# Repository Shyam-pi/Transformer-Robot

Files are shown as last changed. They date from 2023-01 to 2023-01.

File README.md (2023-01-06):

# Transformer-Robot
A novel mobile manipulator with a collapsible arm created for my final project of ENPM662 at the University of Maryland, College Park

Please find the CAD model of the robot in CAD_model.zip 

To run the ROS/URDF package in Gazebo, extract the transformers.zip folder to your catkin workspace, and do the following to build it: 
1. Navigate to your catkin workspace folder, open terminal and enter 'catkin_make' to build the workspace.
2. Enter the following command in your terminal 'source ~/catkin_ws/devel/setup.bash'

Once the building process is done, you can simply launch the package in Gazebo by using the following command in your terminal:
roslaunch transformer template.launch

In order to visualize the feed from the camera, after executing the above command, type 'rviz' in a new terminal window. In your RVIZ, add an 'Image' component, and change the image topic to the available topic, and you can see the video feed from the camera appearing in a window in Rviz.

To launch any of the ROS python scripts, navigate to the scripts folder inside the package, and open a terminal window in that location. Launch any of the available scripts using the below command in terminal 

python3 'script_name.py'

Please take note that you need to use any of the scripts only when Gazebo is running, and terminal window should overlay on top of the Gazebo window.

Following are the description of the available scripts:

1. teleop.py - Use this script to control the mobile base of the robot.
2. publisher.py - It is used to initialize the configuration of the robot. Type 0 followed by the publisher.py to take the robot to collapsed position, and 1 to take it to the extended position.

Please checkout the outputs folder for visualizing the working of the package.

To get comprehensive information on the robot please refer to the report available in the repo.

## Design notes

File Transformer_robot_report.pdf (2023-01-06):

## ENPM662 - Introduction to Robot Modeling

## Project 2 Modeling of Transformer Robot

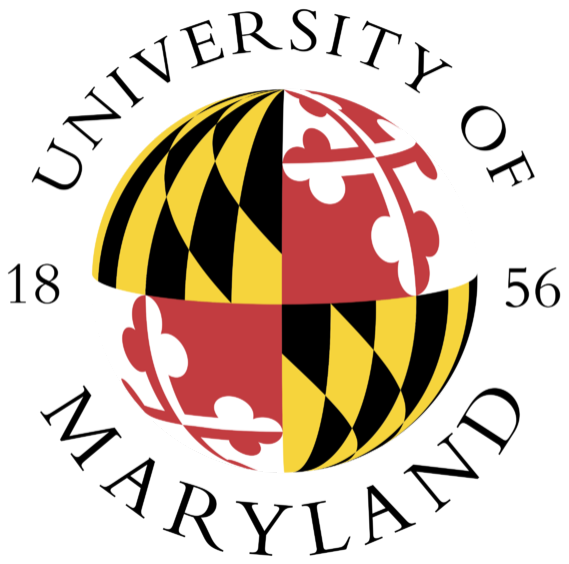
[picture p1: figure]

AUTHOR:
SHYAMSUNDAR PRABHAKAR INDRA UID - 119360842
DIRECTORY ID - SHYAMPI

ii

### ABSTRACT

This project explains the design, control, and simulation of a novel ’Transformer Robot’ which can potentially make a huge difference of how storage systems work, which can especially be a huge game-changer in today’s world with the amount of products being produced everyday. The robot consists of a mobile base and a manipulator arm, which were designed using Solidworks[1] and were exported as a URDF. A ROS[2] package was developed, with transmissions and controllers, and integrated with the URDF. A camera was attached to the end effector of the manipulator arm to visualize the environment. The forward and inverse kinematics of the robot’s arm are calculated and verified. The robot has been simulated and controlled in Gazebo. A simulation of the robot doing a planned task in a custom environment has also been done. The challenges faced and future work planned have been described.

iii

### TABLE OF CONTENTS

iv

### LIST OF ILLUSTRATIONS

Number | Page
1.1 Conventional Forklift in a Storage House[3] | | 2
3.1 Transformer Robot in its extended mode | | 5
3.2 Transformer Robot in its collapsed mode | | 6
3.3 Manipulator Arm extended mode | | 7
3.4 Manipulator Arm collapsed mode | | 7
3.5 Close-Up of End Effector | | 8
4.1 Coordinate Systems assignment | 10
5.1 Representation of case 1 in Gazebo | 13
5.2 FK Validation for Case 1 | 14
5.3 Representation of case 2 in Gazebo | 14
5.4 FK validation for Case 2 | 14
5.5 Initialized Jacobian Matrix and corresponding robot pose | 15
5.6 Trajectory traced using Jacobian in python script | 16
5.7 Variation of joint parameters with time, to achieve the trajectory . . . 16
6.1 Workspace of the Robotic Arm in ’mm’ | 17

C h a p t e r 1

### INTRODUCTION

Mobile Manipulators aren’t a rarity in today’s technologically advanced world. However almost all the mobile manipulators one can come across are pretty tall in z-height, if not for their large overall size. One classical example is that of the Husky UGV with its tall Manipulator arm sticking out.

Contrary to such tall mobile manipulators, a novel ’Transformer Robot’ is being introduced. Getting its name from the famous Transformers cartoon, it is indeed yet another Mobile Manipulator, but quite different. The Transformer Robot has a collapsible arm, i.e., the manipulator arm is custom designed such that in it’s ’collapsed’ state it’s almost in level with the mobile base itself.

Such a robot with a reduced z-height, opens up to a plethora of opportunities. One of the most prominent is the way storage industries work. Conventionally such storage houses have pre-defined long pathways for the forklifts to move in a very inefficient manner as shown in figure 1.1. The Transformer robot can potentially revolutionize the way such storage houses work. When provided with shelves with a gap underneath, the Transform Robot with it’s low-profile could easily navigate through these gaps, hence reducing the distance covered in the to and fro motion to a great level. Though this feels trivial, when looked at this over a period of years and years, this shall save thousands of hours and miles of extra work. This motion efficiency, can boost the energy efficiency of these places as well.

This project report describes the work done in designing, controlling, and simulating the above proposed Transformer Robot. The report is divided into various sections. The introduction provides an overview of the Transformer Robot and its novel applications. The detailed specifications of the Transformer Robot are described in the section titled "The Transformer Robot" The "Kinematics and Kinematic Validation" section covers the forward and inverse kinematics of the robot’s manipulator arm and the validation of the calculations. The "Workspace Study" section discusses the total reach of the arm and the limitations of the space it cannot reach. The "Assumptions" section outlines the assumptions made during the development and design of the Transformer Robot. The "Package, Control Method and Visualization" provides a link to the entire working package itself,

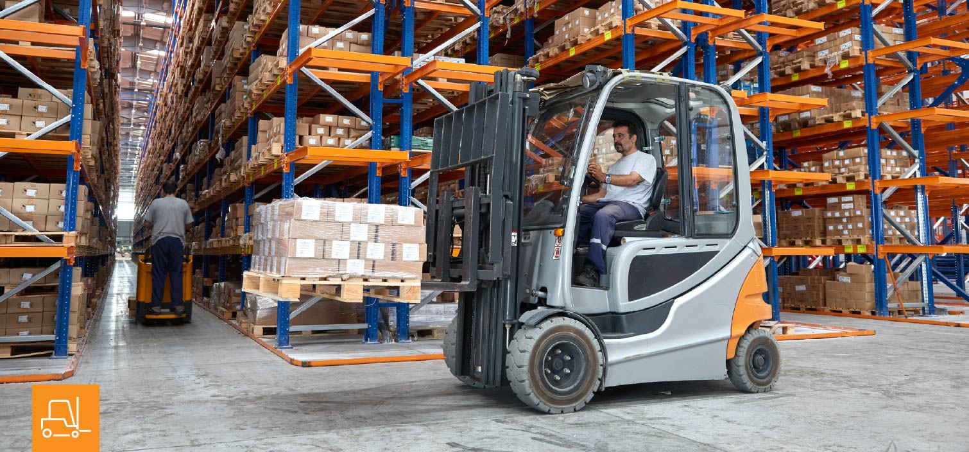
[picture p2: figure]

Figure 1.1: Conventional Forklift in a Storage House[3]

the way the joints in the robots are controlled, and a visualization of the robot performing a specific task. The "Problems Faced and Lessons Learned" section covers the challenges encountered during the project and the lessons learned from them. The "Future Work" section lists potential improvements to the Transformer Robot. The "Conclusion" section summarizes the project, and the "References" section lists the sources used.

C h a p t e r 2

### THE TRANSFORMER ROBOT

This section briefs the proposed design, specifications, and the planned task of the robot being modeled for this project.

### 2.1 Specifications of the Transformer Robot

Mobile Base
Length of the Mobile Base | 0.914 m
Width of the Mobile Base | 0.508 m
Height of the Mobile Base | 0.3 m
Mass (Base + Wheels + Axles) | 82.6 Kg
Wheel Base | 0.508 m
Motion Model | Unicycle
Degrees of Freedom | 3 in total - x, y and yaw.
Manipulator Arm
Height of Arm with all joints extended | 2.388 m
End Effector Used | Simple custom 1 DOF Grasping tool
Degrees of Freedom | 7 in total - Five revolute and one pris-matic, and one DoF for the End Effector
Length of End Effector | 0.09 m

### 2.2 Type of Robot

The type of robot used here is a mobile manipulator. Mobile manipulators are used in several applications all over Earth and even beyond Earth. For example, Husky UGV is a mobile manipulator which is used for all-terrain Robotics research, and a Mars rover is also a type of mobile manipulator. The manipulator arm is a serial manipulator.

### 2.3 Degrees of Freedom of The System

The system has a total of 9 DoF. The mobile base has 3 DoF while the manipulator arm has 5 DoF. The mobile base can move along x and y directions and rotate around the z axis. The arm has 3 revolute joints, with a prismatic joint and revolute joint for the end-effector, and the end-effector itself has 1 DoF.

### 2.4 Application of The Transformer Robot

As the introduction described, the robot is a novel attempt at reforming how storages work. Conventionally, most of the storage houses use forklifts operated by humans, which have to navigate through longer pathways. The central idea behind the Transformer robot is a mobile manipulator being able to reduce the vertical height of itself so that it can easily navigate through remote spaces.

The proposed idea of reformed storage systems is that the shelves have ample space underneath them, enough for the transformer robot to pass through in their collapsed state. This will allow the transformer robot to navigate to the point of interest in the shortest way possible, hence saving thousands and thousands of man-hours and power in the long run.

### 2.5 Motivation for Choosing Transformer Robot

The main motivation was the novelty behind the transformer robot, which enables it to be used as a multi-purpose robot which, as explained before, can be used for efficient pick and place operations and at the same time, owing to its small size in its collapsed state, and can be used for search and rescue operations having acces to remote areas in case of anomalies at the same time.

The project presented an opportunity to create a holistic model right from basic 3D modelling to actually making a simulation of the same. The idea of modelling what was learnt in the theory into an actual working model from scratch was also a great motivation for the choice.

C h a p t e r 3

### CAD MODELS

This section contains pictures of the Transformer Robot assembly and that of the manipulator arm assembly in its two different modes.

### 3.1 The Transformer Robot CAD Model

The model of the Transformer Robot was created from scratch using Solidworks. The Robot’s two modes are shown in figure 3.1 and figure 3.2.

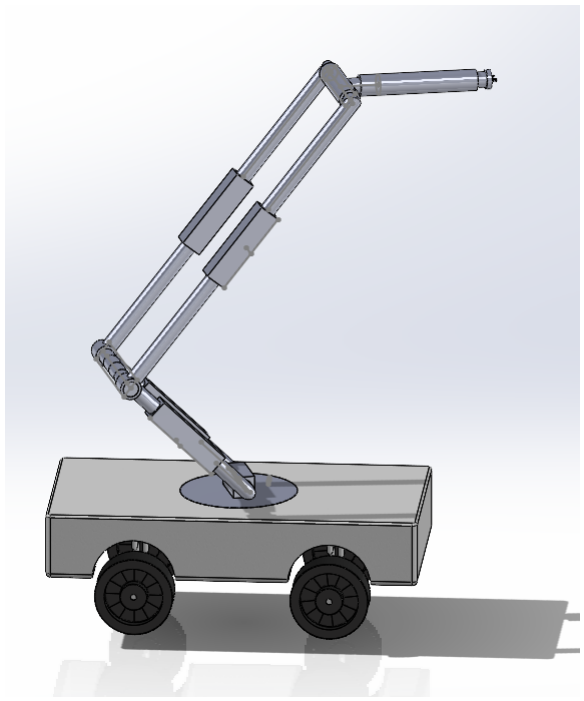
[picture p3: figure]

Figure 3.1: Transformer Robot in its extended mode

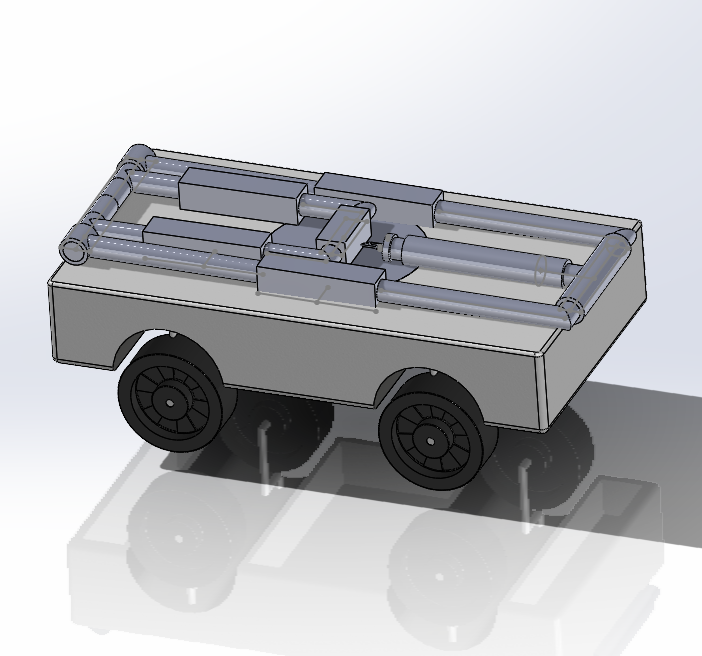
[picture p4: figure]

Figure 3.2: Transformer Robot in its collapsed mode

### 3.2 The Arm Model

This section has two views of the arm model as well as a close up of the custom designed end effector as shown in figure 3.3 and figure 3.4. The arm model has a rotating base which is attached to the mobile base, allowing full freedom of revolution. This joint is followed by three revolute joints with their rotation axis parallel to each other. Hence the arm itself has 6 degrees of freedom. This is followed by a prismatic joint, revolute joint and then the end effector.

The end effector is a simple setup with two fingers, each having a revolute joint tied to each other, hence having 1 DoF in total.

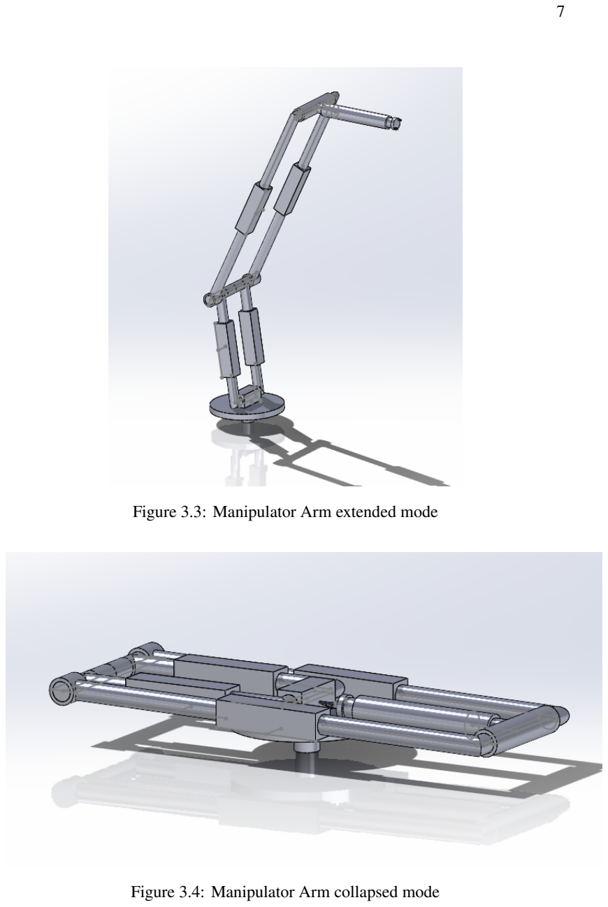
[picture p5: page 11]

Figure 3.3: Manipulator Arm extended mode

Figure 3.4: Manipulator Arm collapsed mode

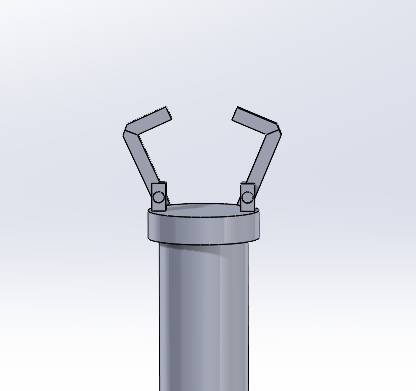
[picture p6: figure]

Figure 3.5: Close-Up of End Effector

C h a p t e r 4

### KINEMATICS

### 4.1 Forward Kinematics

Forward Kinematics is the computation of the end effector position given the joint angles at each joint. The Forward Kinematics is calculated only for the manipulator arm, assuming that it’s mounted on top of a fixed base (Mobile base’s wheels are fixed). The following steps are involved in calculation of the Forward Kinematics for the manipulator arm:

- Assigning the frames at each joint
- Finding the D-H table
- Calculating the Final Transformation Matrix

The manipulator of the Transformer robot has 6 degrees of freedom excluding the end effector, and the first joint is not the ground frame. Therefore 8 frames are required to describe the manipulator arm, 6 for the joints, 1 for ground frame and 1 for the end effector frame. However when formulating the DH[4] table, it was observed that it was necessary to introduce two dummy frames in order to successfully satisfy DH constraints. The assigned frames are as shown in Figure 4.1

The D-H table is calculated by using the assigned frames and the calculated D-H table is shown in Table 1. The D-H table is calculated by following the rules:

- θn is the rotation at the revolute joints
- q is the linear displacement at the prismatic joint
- an is the distance between the Zn−1 and Zn (along Xn axis)
- dn is the distance between the On−1 and intersection of Zn−1 and Xn along

Zn−1 axis

- αn is the angle between Zn−1 and Zn measured around Xn

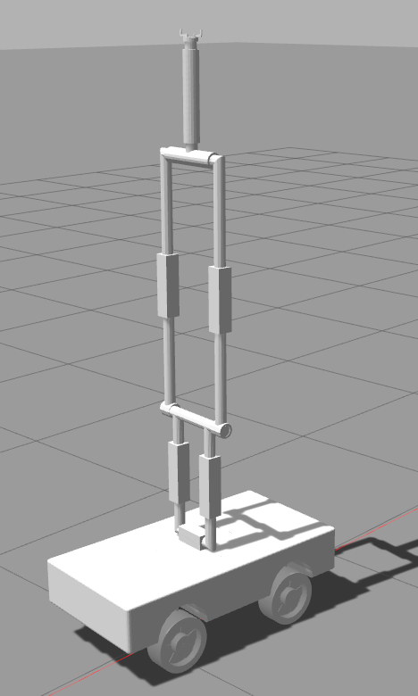
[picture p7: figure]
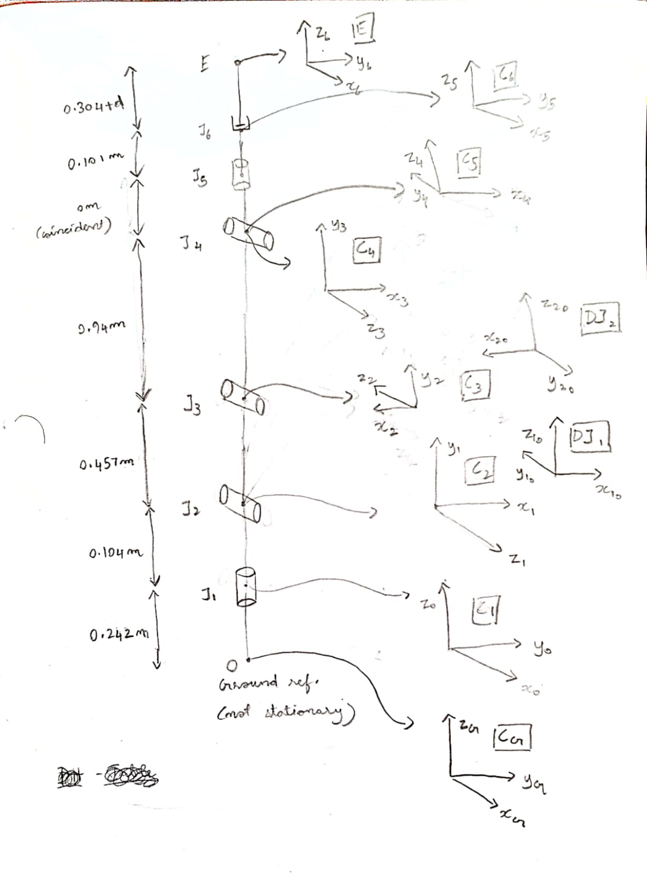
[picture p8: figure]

Figure 4.1: Coordinate Systems assignment

D-H TABLE

| α | θ | d | a
G - 0 0 - 1 1 - 10 10 - 2 2 - 20 20 - 3 3 - 4 4 - 5 5 - 6 | 0 π/2 −π/2 −π/2 π/2 π/2 −π/2 0 0 | 0 θ1 θ2 0 θ3 0 θ4 θ5 0 | 0.242 0.104 0 0.457 0 0.94 0 0.101 0.304 + q | 0 0 0 0 0 0 0 0 0

Then using the D-H table and the assigned frames the final transformation matrix was calculated which gives the pose and orientation of the end-effector. To find the final transformation matrix we have to follow the following steps:

1. Individual Transformation matrices are to be found (i.e.) T

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
5/4 and T

6
5
2. The individual transformation can be found by plugging in the joint angle values and the rest of the values from the D-H table given above into the below matrix:
cosθi | −sinθicosαi | sinθisinαi | aicosθi
sinθi | cosθicosαi | −cosθisinαi | aisinθi
0 | sinαi | cosαi | di
0 | 0 | 0 | 1
3. The final transformation can be found by multiplying all the individual transformation matrices in the format given below

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
The Final transformation matrix after all the computations is shown is too long to be shown as an image. Please follow this link to the Google Colab notebook to see the printed Final Transformation matrix:

FK and IK Results (https://colab.research.google.com/drive/1XfMuMxmm27r3gcsec8usFtIJDnRUijgn?authuser=1)

### 4.2 Inverse Kinematics

In Inverse Kinematics, we do the reverse of Forward Kinematics by calculating the joint angles by using a known end-effector position. One can either calculate one of these or both, for Inverse Kinematics :

- Inverse Position Kinematics
- Inverse Velocity Kinematics

For the case of the Transformer robot, the inverse velocity kinematics were computed by calculating the Jacobian. To find the joint angles by using the end-effector position one has to follow these steps:

1. Finding all the individual Transformation matrices and the final transformation by multiplying them
2. Find Zi which are the column matrices containing the elements of the 3

r d

column in the Ti matrix

3. After finding the Zi matrices, Then find the Xpi matrices which contain the elements from the last column of each individual matrices
4. Differentiate the matrices Xp1, Xp2, Xp3 and Xp4 with respect to the joint angles θ1, θ2, q3 and θ4 respectively
5. Then form the individual Jacobian matrices in the format given below

0
Jn =

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
0Z1 ...

0Zi

0Zn

The resultant Jacobian is too big to be fit into a screenshot since it’s a 6 DoF manipulator. Find the printed parametric Jacobian in the attached Google Colab notebook below:

FK and IK Results (https://colab.research.google.com/drive/1XfMuMxmm27r3gcsec8usFtIJDnRUijgn?authuser=1)

C h a p t e r 5

### KINEMATIC VALIDATIONS

### 5.1 Forward Kinematics Validation

For validating the forward kinematics of the manipulator arm, two sets of joint parameters were inputted to the manipulator arm in Gazebo, and the respective end effector positions in Gazebo were noted down. The same joint parameters were inputted to the final transformation matrix computed in section 4.1, and the respective end effector positions were obtained from the last column of the resultant transformation matrix.

Joint parameters set 1 = [0, 0, 0, 0, 0, 0]
Joint parameters set 2 = [0, 0, π/2, π/2, 0, 0]

The position vector from the above two steps for both the cases of joint parameter sets are shown below:

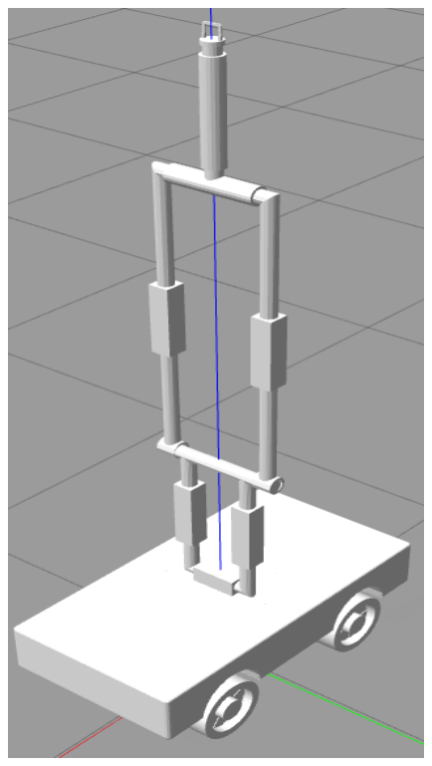
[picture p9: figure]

Figure 5.1: Representation of case 1 in Gazebo

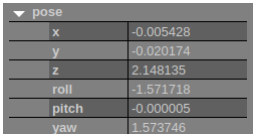
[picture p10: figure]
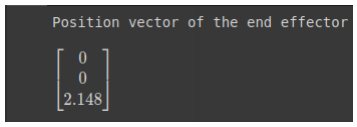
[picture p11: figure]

Figure 5.2: FK Validation for Case 1

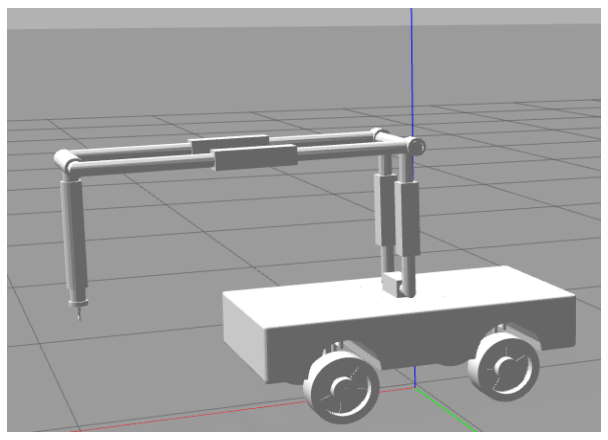
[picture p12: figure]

Figure 5.3: Representation of case 2 in Gazebo

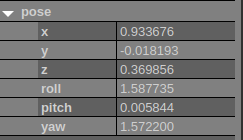
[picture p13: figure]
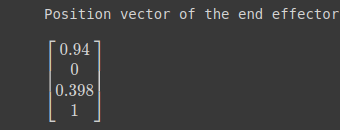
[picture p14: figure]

Figure 5.4: FK validation for Case 2

### 5.2 Inverse Kinematics Validation

The validation of the inverse kinematics part was done by plotting a straight line of length 0.2 metres along the z-axis direction in 100 seconds (so that the process is quasistatic). A python script was created to do the same by following the below steps:

1. After finding the final parametric Jacobian matrix in 4.2, the initial angles of the manipulator before the validation are given as input, and the hence the initial Jacobian is populated.
2. In this case, the Jacobian is a square 6x6 matrix, hence there is no need for pseudoinverse. A small value of delta = 1e-6 is added to all elements of the Jacobian before taking inverse, in order to avoid any singular matrix errors.
3. Compute X¤ according to the trajectory intended to trace. In this case X¤ only

had a constant z velocity component.

4. Then find the Q¤ matrix by multiplying the inverse jacobian matrix and the X¤ matrix, where (X¤ matrix is the matrix that contains the linear and angular

velocity components of the end effector)

5. The Q¤ matrix contains the values of the joint angles and those values are

obtained and numerical integration is performed to get the corresponding joint angle values for every time step.

6. These computed joint angles are then used as an input to the final Transformation matrix from 4.1, and the end effector position is obtained at every time step
7. The so obtained end effector positions are plotted as a 3D plot and visualized. As seen below, the resultant trajectory traced is a straight line as intended.

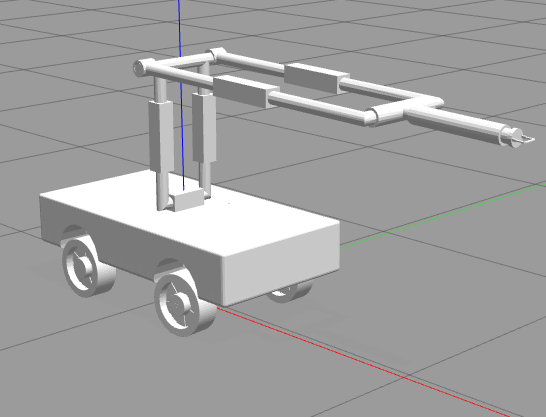
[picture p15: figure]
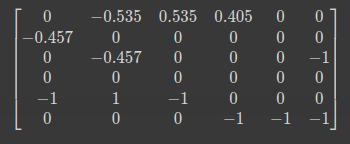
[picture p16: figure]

Figure 5.5: Initialized Jacobian Matrix and corresponding robot pose

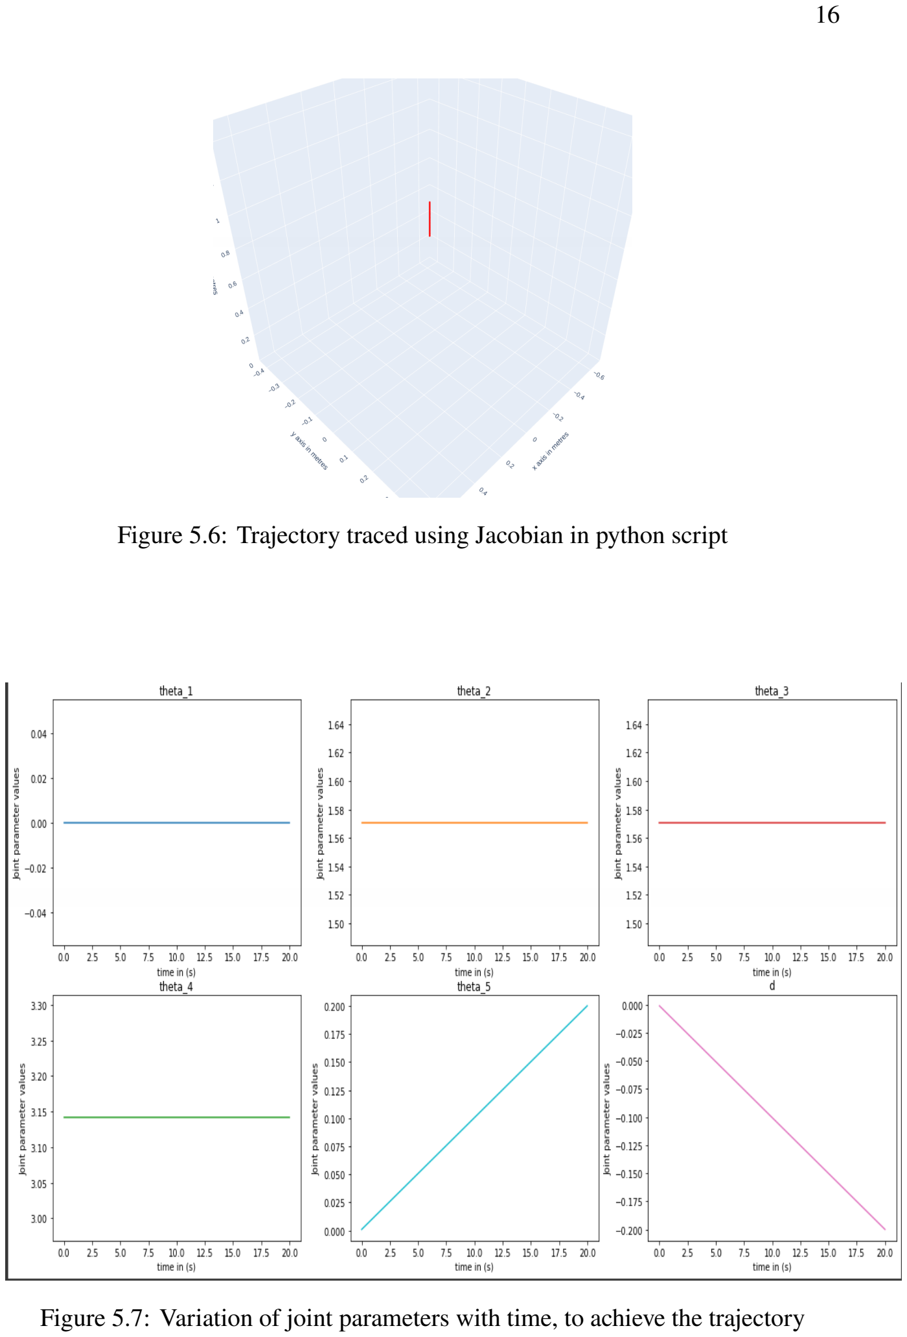
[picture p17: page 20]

Figure 5.6: Trajectory traced using Jacobian in python script

Figure 5.7: Variation of joint parameters with time, to achieve the trajectory

C h a p t e r 6

### WORKSPACE STUDY

The workspace study was done for only the manipulator arm by fixing the mobile base (making the wheels static). The workspace of the manipulator arm is a hemisphere of radius 2.25 metres, centred at the origin.

The first revolute joints allows a full 360 degree rotation along the global z axis, and the second revolute joints let’s the whole manipulator make a 180 degree sweep, hence achieving a hemisphere. Due to the redundant number of joints, the end effector can actually reach below the plane containing the first joints coordinate axes.

Analytically the reach of the arm was found out by using the parametric end effector position from the final transformation matrix. This was followed by fixing every joint parameter except for θ1 and θ2, which were made to sweep [0,360] and [-90,90] degrees respectively, and the point clouds as a result of the sweep were plotted in a 3D plot. The below figure shows the reachable workspace of the manipulator arm.

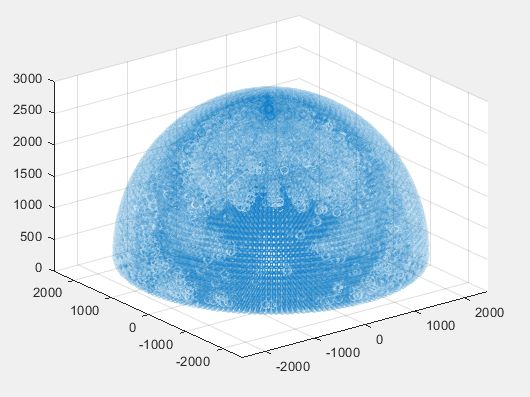
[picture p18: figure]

Figure 6.1: Workspace of the Robotic Arm in ’mm’

C h a p t e r 7

### ASSUMPTIONS

The following are the assumptions made to make a successful model of the transformer robot, and thereby verify its Forward and Inverse Kinematics:

- All the Kinematics computations for the manipulator arm in its extended state.
- All input parameters were within the range of motion allowed by every joint.
- Although the 3D model of the wheel is smooth, there is friction acting between

the wheels and the Gazebo world.

- External forces like friction have not been considered.
- Throughout the period of validation, the mobile base is docked, i.e., zero

motion in the mobile base.

- Self collisions between parts of the robot arm were turned off.
- The weight of the mobile base is enough to not let the robot topple at any

orientation of the manipulator arm.

C h a p t e r 8

### PACKAGE, CONTROL METHOD AND VISUALIZATION

### 8.1 Package

The package containing all the necessities to spawn and run the transformer robot in Gazebo can be found in the link to my Github repository found below

Repository Link (https://github.com/Shyam-pi/Transformer-Robot)

The repository also contains the 3D models (including the part and sldasm files) of the Transformer Robot. The instructions to run the ROS package itself can be found in the readme file of the repository.

### 8.2 Control Method

The mobile base of the Transformer robot consists of 2 revolute joints for the steering, and 4 continuous joints for the wheels. The 2 revolute joints for the steering were controlled with Joint position controllers and the two continuous joints of the rear wheel were controlled using Velocity controllers.

For the manipulator arm, there are 5 revolute joints and 1 prismatic joint for the arm itself and 2 revolute joints for the fingers of the end effector. All these joints are controlled using Joint Position controllers.

All the Joint Position controllers needed careful tuning of the PID values[5], without which there was jittering or abrupt motion in the joints. Different joints needed different PID values especially according to the mass and inertia of the link they were controlling.

Controllers YAML file link (https://drive.google.com/file/d/1ZQy9Z_QbMUzOGTrWu4JHJh3Bh8IsT9NB/view?usp=share_link)

### 8.3 Simulation

The spawing and simulation of the transformer robot was done using Gazebo. The video of the same can be found in the following folder:

Simulation video link (https://drive.google.com/drive/folders/1r95u0Vq24YU3A0hC_s1uwHW8knL1vMpW?usp=share_link)

C h a p t e r 9

### PROBLEMS FACED AND LESSONS LEARNED

Extremely unstable Ubuntu OS, which I had to reinstall twice during the duration of this project. I had to keep it open for 2 days straight so that there are no last minute risks. Buggy URDF import plugin and several Ubuntu and Gazebo woes. PID controller tuning, which was very difficult for parts of low mass like that of the end effector fingers. Idle drift in Gazebo which is a known issue, which does not have a readily available foolproof fix. Due to the presence of long narrow links, the effect of geometry when actuating these was very difficult to deal with, and required precise tuning of the PID. Had to account for sudden jerks caused by the controllers, by doing trajectory planning and slowly actuating, hence making it a quasistatic process.

### 9.1 Problems Faced

This section gives an overview of the number of problems I came across when trying to implement the project.

Instability of the Ubuntu OS
There was some extreme instability with the installed Ubuntu OS in my laptop, which ended up crashing and stopping the detection of GPU and wifi adapter thrice during the duration of the project.

Lack of teammate
Due to the lack of a teammate due to unforeseen reasons, the project became infinite times harder. This was made worse by my choice of doing everything in the project from scratch.

Buggy URDF Export
The URDF export was extremely buggy. I had to go through some 6 iterations of URDF generation and visualizing it in Gazebo before I got it to work properly. For example, once it automatically changed the axes defined for the mobile base’s wheels, due to which the mobile base stopped moving. This other time, upon exporting the URDF, the plugin decided to replace the mesh of every part of the robot with a single link’s mesh file and the resultant model wasn’t a sight to behold.

PID Values tuning
The PID tuning for very small parts like that of the end effector fingers was very difficult since the response was extremely sensitive. Whereas for the long parts, PID tuning was extremely difficult due their length and mass, which made them to bounce back and forth before settling at the required joint position.

Sudden Jerks in Joints
High D value in the PID controllers caused sudden jerks when actuating the manipulator. This situation was alleviated by slow trajectory planning, hence making actuation a quasistatic process.

Difficult D-H setup
The created arm for the manipulator arm ended up giving a DH table that was very difficult to formulate. The DH table ended up needing one shift of axes and creation of 2 dummy joints for properly describing the system.

### 9.2 Lessons Learnt

The project ended up being an extremely steep learning curve especially with time management. The experience of creating a custom model from scratch gave a great learning experience with Solidworks, and URDF import. I also learned how to properly interpret a URDF file, even to the extent of modifying intrinsic parameters of each link to make the model work successfully. Post that, the project also gave a great insight into the working of ROS, writing subscriber and publisher nodes, and programming ROS controllers for every joint of the robot and controlling it using ROS topics and messages.

Especially in the forward and inverse kinematics section, I learned a lot by creating a DH table for the custom manipulator arm model and verifying its Kinematics. It provided hands on experience of transferring the theoretical knowledge gained in ENPM662, to a working simulated model. This process, though tedious, taught me how to correctly assign frames, shift origins, and use dummy frames even for complex systems, as any errors in these steps caused discrepancies between theoretical and simulated values. Choosing controllers for the model’s joints also proved to be a challenging lesson, as making incorrect choices resulted in unexpected behaviors when the model was spawned and controlled in Gazebo.

C h a p t e r 10

### FUTURE WORK

The project was successfully completed, but there is potential for further improvements in the future. Some ideas for improvement include performing more in depth analysis and addressing minor issues, which can make the transformer robot move a step closer to becoming a real robot in the storage industry. Some of the work I plan to do in the future includes:

- Performing stress analysis in ANSYS Mechanical which is crucial in this case

because of Transformer Robot’s slender arms

- Adding a LIDAR sensor to the end effector link, so that the end efffector gets

a better imaging of what’s in its surroundings.

- Increase the Degree of Freedom of the arm so that it can execute more range

of motion for various tasks.

- Adding a rotating assembly with multiple tools as the end effector for doing

different tasks.

- Adding more cameras especially one to the chassis of the mobile base which

would help in successful navigation of the robot.

- Add more sensors to the robot to collect more information about the environ-

ment it is in.

- Implementing autonomous navigation for the robot from a start point to a

target point.

- Adding a more efficient path planning algorithm rather than just using Inverse

Kinematics.

C h a p t e r 11

### CONCLUSION

The project was successfully completed, including the study of a novel transformer robot in a virtual environment and its mathematical formulation. The design, simulation, and control of the robot were all successful, and the forward and inverse kinematics were calculated and verified via simulation. The learning outcomes listed in the report were covered, and the project met its goals.

However, some fallback goals, such as simulating the robot in a simpler world and designing the arm with lower number of sensors had to be adopted. The ambitious goals will be part of future work. The project provided a solid understanding of the modeling and control of a complicated mobile manipulator, which could potentially be useful in storage houses for efficient processing, and change the way storage houses work. I also gained skills that can be applied to similar real-time applications and entry-level experience with ROS and Gazebo. I am very thankful to Prof.Reza and the TAs who made this amazing learning experience possible.

### REFERENCES

[1] Solidworks. https://www.solidworks.com/. [Online].
[2] Robotic Operating System. https://www.ros.org/. [Online].
[3] forkliftimage. https://www.catlifttruck.com/products/warehouse-equipment. (https://www.catlifttruck.com/products/warehouse-equipment) [Online].
[4] DH Parameters. https : / / www . researchgate . net / publication / 262166607_Identification_of_Denavit-Hartenberg_Parameters_ of_an_Industrial_Robot. (https://www.researchgate.net/publication/262166607_Identification_of_Denavit-Hartenberg_Parameters_of_an_Industrial_Robot) [Online]. 2013.
[5] PID tuning. https://realpars.com/pid-tuning/. [Online].

A p p e n d i x A

### PYTHON CODE

Python Code for Kinematics validation of Robotic arm

# -*- coding: utf-8 -*-

"""ENPM662_project2_code_shyampi.ipynb

Automatically generated by Colaboratory.

Original file is located at

https://colab.research.google.com/drive/1XfMuMxmm27r3gcsec8usFtIJDnRUijgn

##ENPM662 - Project2 Kinematics code

"""

import numpy as np

from matplotlib import pyplot as plt

from matplotlib.animation import FuncAnimation

from matplotlib import rc

from pprint import pprint

import sympy as sym

from sympy import cos as c

from sympy import sin as s

from sympy import Eq, MatMul, Function, diff

from sympy.matrices import Matrix

from IPython.display import display, Math

import plotly.graph_objs as go

def vis3D(EE_positions):

X = np.array(EE_positions)

print(X.shape)

trace = go.Scatter3d(

x = X[:,0], y = X[:,1], z = X[:,2],mode = ’markers’, marker = dict(

size = 1,

color = ’red’, # set color to an array/list of desired values

colorscale = ’reds’

)

)

fig = go.Figure(data = [trace])

fig.update_layout(

scene = dict(

xaxis = dict(nticks=10, range=[-3,3], title = "x axis in metres"),

yaxis = dict(nticks=10, range=[-2,2], title = "y axis in metres"),

zaxis = dict(nticks=10, range=[-2,2], title = "z axis in metres"),),

width=1000,

height=1000,

margin=dict(r=20, l=10, b=10, t=10))

fig.show()

"""#Problem 1 : Position Kinematics - Panda"""

theta, d, alpha, a = sym.symbols(’theta d alpha a’, real = ’True’)

theta1, theta2, theta3, theta4, theta5, theta6, theta7 = sym.symbols(’theta1 theta2 theta3 theta4 theta5 theta6 theta7’, real = ’True’)

d1, d3, d5, d7, a3 = sym.symbols(’d1 d3 d5 d7 a3’, real = ’True’)

# thetadot1, thetadot2, thetadot3 = sym.symbols(’thetadot1 thetadot2 thetadot3’, real = ’True’)

T = Matrix([[c(theta), -s(theta)*c(alpha), s(theta)*s(alpha), a*c(theta)],

[s(theta), c(theta)*c(alpha), -c(theta)*s(alpha), a*s(theta)],

[0, s(alpha), c(alpha), d],

[0, 0, 0, 1]])

print("General Transformation Matrix in DH system: \n")

T

"""#Individual Transformation Matrices:"""

TG0 = T.subs([(a, 0), (alpha, 0), (d, 0.242), (theta, 0)])

print("Transformation matrix from frame 0 to G:\n")

TG0

T01 = T.subs([(a, 0), (alpha, sym.pi/2), (d, 0.104), (theta, theta1)])

print("Transformation matrix from frame 1 to 0:\n")

T01

T11_ = T.subs([(a, 0), (alpha, -sym.pi/2), (d, 0), (theta, theta2)])

print("Transformation matrix from frame 3 to 2:\n")

T11_

T1_2 = T.subs([(a, 0), (alpha, -sym.pi/2), (d, 0.457), (theta, 0)])

print("Transformation matrix from frame 4 to 3:\n")

T1_2

T22_ = T.subs([(a, 0), (alpha, sym.pi/2), (d, 0), (theta, theta3)])

print("Transformation matrix from frame 5 to 4:\n")

T22_

T2_3 = T.subs([(a, 0), (alpha, sym.pi/2), (d, 0.94), (theta, 0)])

print("Transformation matrix from frame 6 to 5:\n")

T2_3

T34 = T.subs([(a, 0), (alpha, -sym.pi/2), (d, 0), (theta, theta4)])

print("Transformation matrix from frame 7 to 6:\n")

T34

T45 = T.subs([(a, 0), (alpha, 0), (d, 0.101), (theta, theta5)])

print("Transformation matrix from frame 7 to 6:\n")

T45

T56 = T.subs([(a, 0), (alpha, 0), (d, 0.304+d), (theta, 0)])

print("Transformation matrix from frame 7 to 6:\n")

T56

"""#Final FK Transformation Matrix"""

TG6 = sym.MatMul(TG0,T01,T11_,T1_2,T22_,T2_3,T34,T45,T56, evaluate = True)

print("Final Transformation Matrix before substituting the length values : \n")

TG6

"""#Geometric Validation

Case 1 - All thetas = 0, d = 0

"""

res = TG6.subs([(theta1, 0), (theta2, 0), (theta3, 0), (theta4, 0), (theta5, 0), (d, 0)])

print("Position vector of the end effector with respect to the ground coordinate system : \n")

res[:-1,3]

"""Case 2 - Theta3 = 90 degrees, and theta4 = 270 degrees. All other parameters 0."""

res = TG6.subs([(theta1, 0), (theta2, 0), (theta3, sym.pi/2), (theta4, 3*sym.pi/2), (theta5, 0), (d, 0)])

print("Position vector of the end effector with respect to the first joint’s coordinate system : \n")

res[:,3]

"""#Validating Inverse Kinematics"""

TG1 = sym.MatMul(TG0, T01, evaluate = True)

TG2 = sym.MatMul(TG1, T11_,T1_2, evaluate = True)

TG3 = sym.MatMul(TG2, T22_,T2_3, evaluate = True)

TG4 = sym.MatMul(TG3,T34, evaluate = True)

TG5 = sym.MatMul(TG4,T45, evaluate = True)

TG6 = sym.MatMul(TG5,T56, evaluate = True)

"""#Populating the parametric Jacobian matrix"""

J = Matrix( sym.symarray(’a’, (6,6)) )

J[-3:,0] = TG1[:-1,2]

J[-3:,1] = TG2[:-1,2]

J[-3:,2] = TG3[:-1,2]

J[-3:,3] = TG4[:-1,2]

J[-3:,4] = TG5[:-1,2]

J[-3:,5] = TG6[:-1,2]

J[0:3,0] = TG6[:-1,3].diff(theta1)

J[0:3,1] = TG6[:-1,3].diff(theta2)

J[0:3,2] = TG6[:-1,3].diff(theta3)

J[0:3,3] = TG6[:-1,3].diff(theta4)

J[0:3,4] = TG6[:-1,3].diff(theta5)

J[0:3,5] = TG6[:-1,3].diff(d)

# J = J.subs([(d1, 0.333),(d3, 0.3160),(d5,0.3840),(d7,0.2070),(a3,0.088)])

print("Printing parametric Jacobian:\n")

J

"""#Quantizing the duration of motion in n time steps, and finding velocity of end effector wrt base frame at every time step."""

steps = 200

t = np.linspace(0,20,steps)

t_step = 20/steps

z_init = 0.773

x_init = 1.347

z_dot = 0.01

vel_origin = np.zeros((6,steps))

vel_origin[0,:] = 0

vel_origin[1,:] = 0

vel_origin[2,:] = z_dot

thetas = np.array([0,sym.pi/2,sym.pi/2,sym.pi,0,0])

J_init = J.subs([(theta1, thetas[0]), (theta2, thetas[1]), (theta3, thetas[2]), (theta4, thetas[3]), (theta5, thetas[4]), (d, thetas[5])])

J_init

thetas = np.array([0,sym.pi/2,sym.pi/2,sym.pi,0,0])

j_angles = []

EE_positions = []

EE_base = TG6

for i in range(steps):

J_step = J.subs([(theta1, thetas[0]), (theta2, thetas[1]), (theta3, thetas[2]), (theta4, thetas[3]), (theta5, thetas[4]), (d, thetas[5])])

J_step = np.array(J_step).astype(np.float64) + 0.00001

joint_vel = np.linalg.inv(J_step) @ vel_origin[:,i]

new_thetas = thetas + t_step*joint_vel

# print(joint_vel.shape)

j_angles.append(new_thetas)

EE_base_temp = EE_base.subs([(theta1, new_thetas[0]), (theta2, new_thetas[1]), (theta3, new_thetas[2]), (theta4, new_thetas[3]), (theta5, new_thetas[4]), (d, new_thetas[5])])

# print(EE_base_temp)

EE_base_temp = np.array(EE_base_temp).astype(np.float64)

EE_position = EE_base_temp[:-1,3]

EE_positions.append(EE_position)

thetas = new_thetas

print("Completed = " + str(i+1) +"/" + str(steps))

j_params = np.array(j_angles).reshape(steps, 6)

fig, axs = plt.subplots(2, 3, figsize = (20,10))

axs[0, 0].plot(t, j_params[:,0]*0)

axs[0, 0].set_title(’theta_1’)

axs[0, 1].plot(t, j_params[:,1], ’tab:orange’)

axs[0, 1].set_title(’theta_2’)

axs[0, 2].plot(t, j_params[:,2], ’tab:red’)

axs[0, 2].set_title(’theta_3’)

axs[1, 0].plot(t, j_params[:,3], ’tab:green’)

axs[1, 0].set_title(’theta_4’)

axs[1, 1].plot(t, j_params[:,4], ’tab:cyan’)

axs[1, 1].set_title(’theta_5’)

axs[1, 2].plot(t, j_params[:,5], ’tab:pink’)

axs[1, 2].set_title(’d’)

for ax in axs.flat:

ax.set(xlabel=’time in (s)’, ylabel=’Joint parameter values’)

import plotly.graph_objs as go

X = np.array(EE_positions)

trace = go.Scatter3d(

x = X[:,0]*0, y = X[:,1]*0, z = X[:,2],mode = ’markers’, marker = dict(

size = 1,

color = ’red’, # set color to an array/list of desired values

colorscale = ’reds’

)

)

fig = go.Figure(data = [trace])

fig.update_layout(

scene = dict(

xaxis = dict(nticks=10, range=[-0.7,0.7], title = "x axis in metres"),

yaxis = dict(nticks=10, range=[-0.45,0.45], title = "y axis in metres"),

zaxis = dict(nticks=10, range=[0,1.5], title = "z axis in metres"),),

width=1000,

height=1000,

margin=dict(r=20, l=10, b=10, t=10))

fig.show()

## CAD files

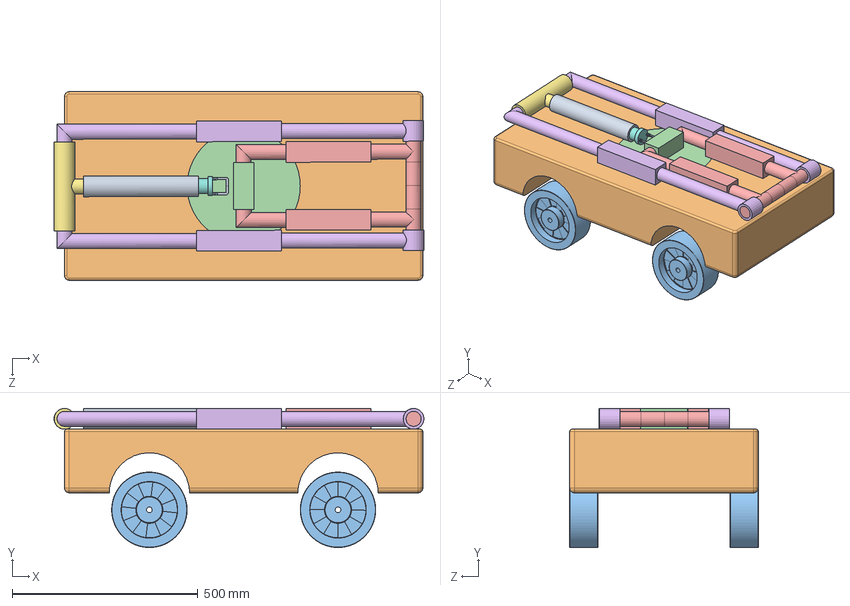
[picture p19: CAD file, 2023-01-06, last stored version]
CAD_Model/transformer.SLDASM
996.4 x 374.6 x 508.0 mm
Chassis
Wheels x 4
rotating_base
link1
link2
final_link3
final_link4
link5
finger x 2

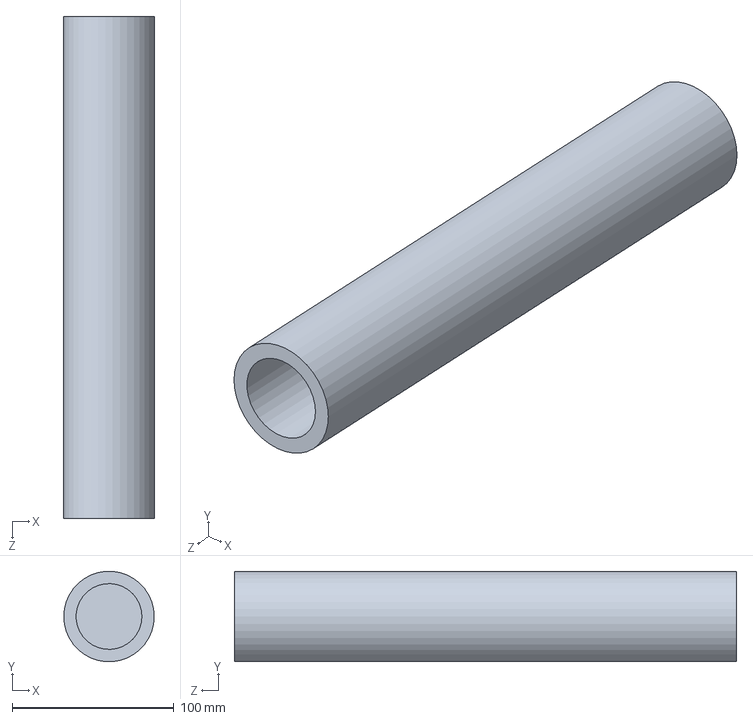
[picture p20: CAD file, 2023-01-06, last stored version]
CAD_Model/final_link4.SLDPRT
55.9 x 55.7 x 309.9 mm

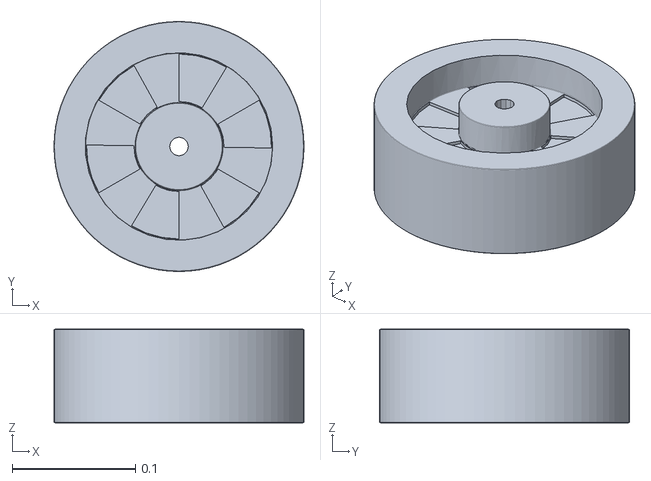
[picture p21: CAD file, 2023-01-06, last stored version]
transformer/meshes/BL_wheel.STL
0.203 x 0.203 x 0.0762

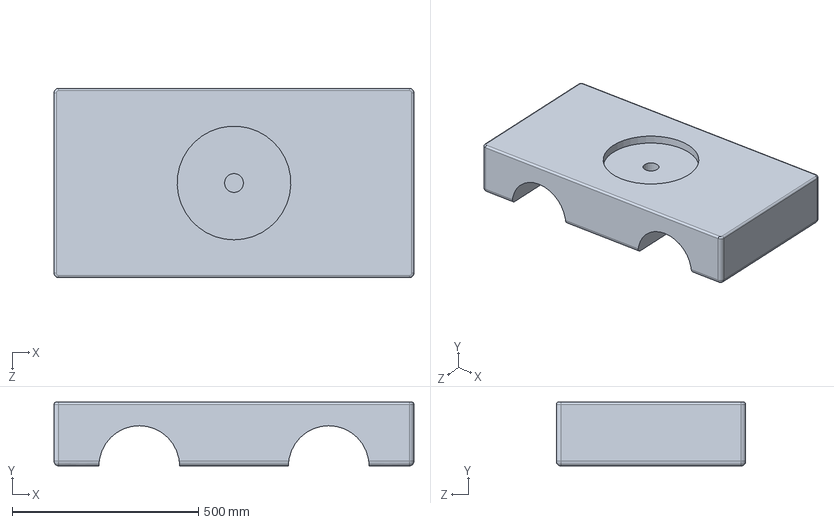
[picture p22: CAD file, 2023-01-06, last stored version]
CAD_Model/Chassis.SLDPRT
965.2 x 171.4 x 508.0 mm

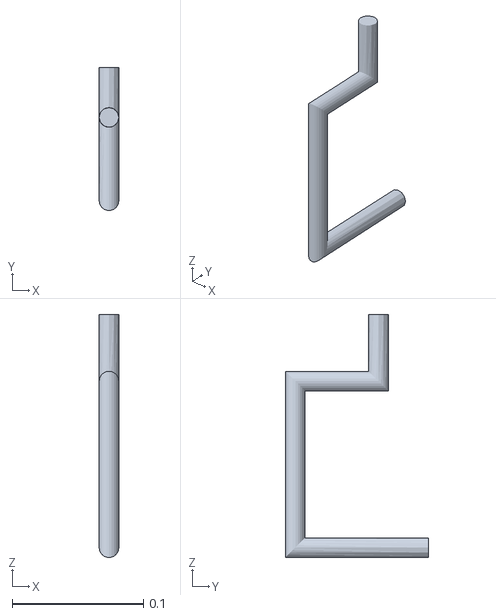
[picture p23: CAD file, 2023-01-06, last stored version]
transformer/meshes/FL_axle.STL
0.015 x 0.109 x 0.185

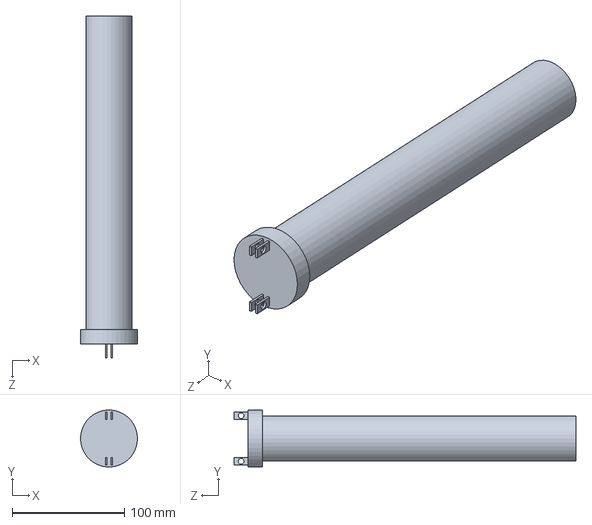
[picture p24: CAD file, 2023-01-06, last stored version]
CAD_Model/link5.SLDPRT
50.8 x 50.6 x 304.8 mm

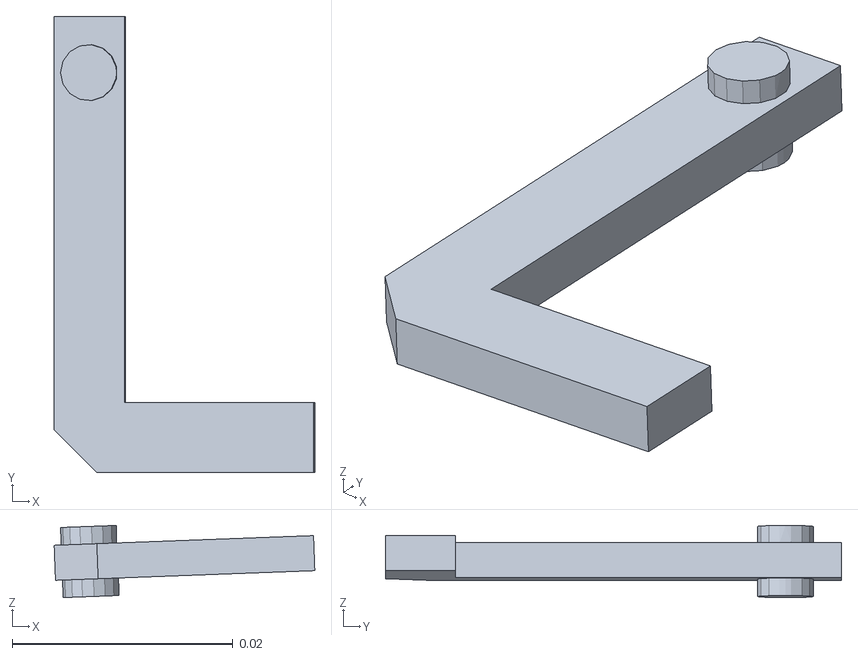
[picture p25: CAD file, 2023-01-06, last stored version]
transformer/meshes/finger1.STL
0.0236 x 0.0413 x 0.00653

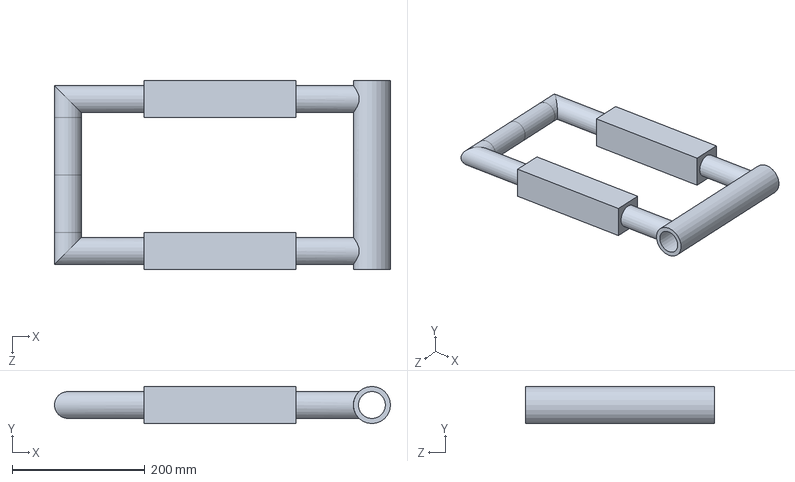
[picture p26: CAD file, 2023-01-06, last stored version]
CAD_Model/link3_new.SLDPRT
505.5 x 55.9 x 284.5 mm

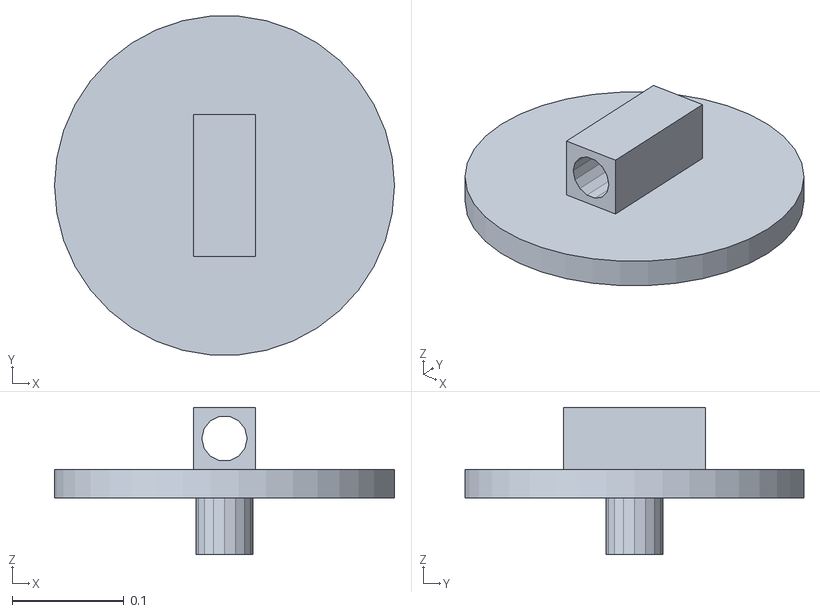
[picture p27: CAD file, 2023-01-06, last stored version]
transformer/meshes/mlr_link1.STL
0.305 x 0.304 x 0.132

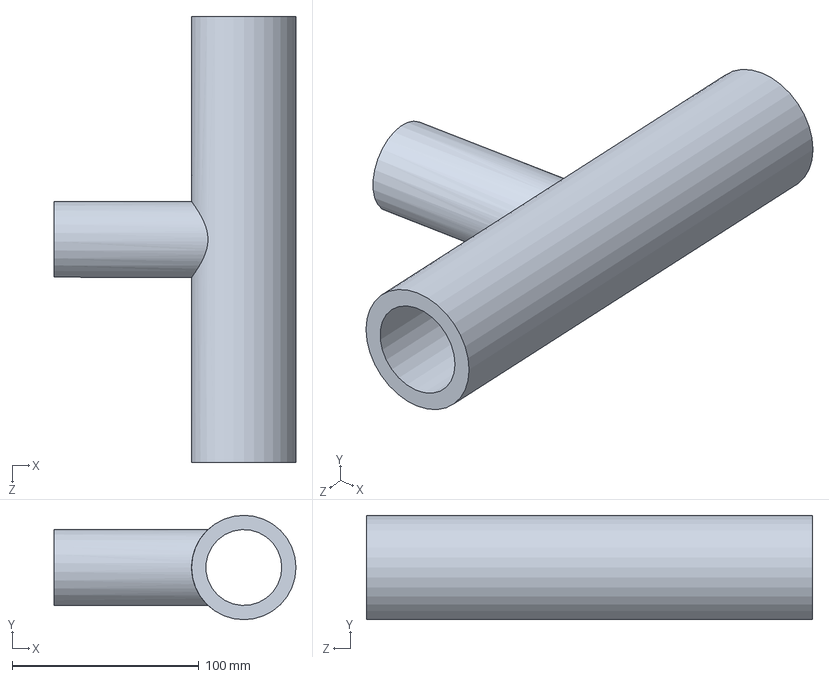
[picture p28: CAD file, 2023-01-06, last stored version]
CAD_Model/final_link3.SLDPRT
129.5 x 55.9 x 238.8 mm

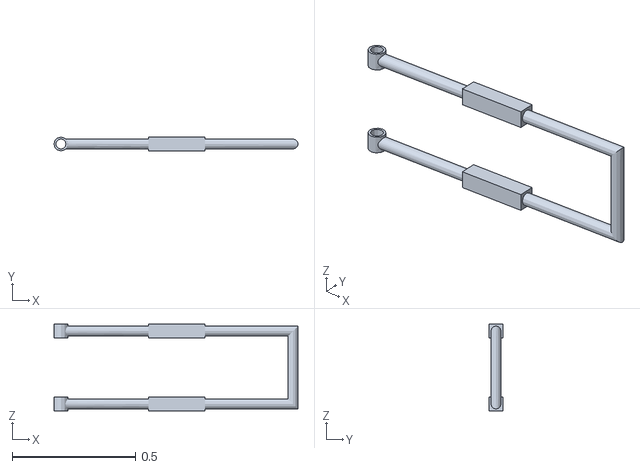
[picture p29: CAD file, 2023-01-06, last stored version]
transformer/meshes/mlr_link3.STL
0.988 x 0.0559 x 0.351

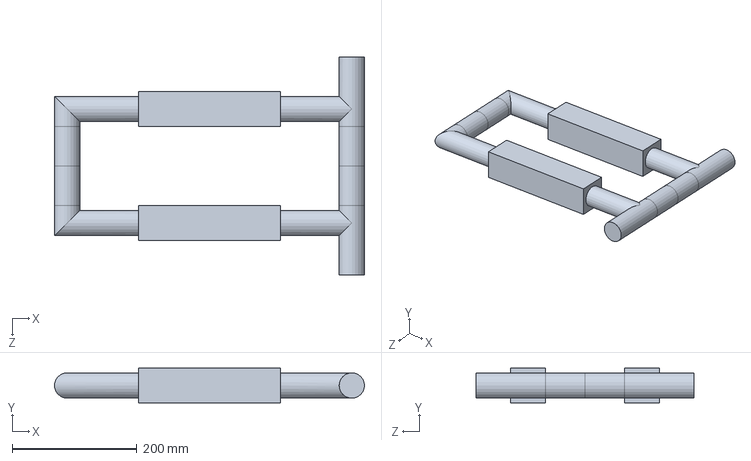
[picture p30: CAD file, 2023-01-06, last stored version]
CAD_Model/link1.SLDPRT
497.8 x 55.9 x 350.5 mm

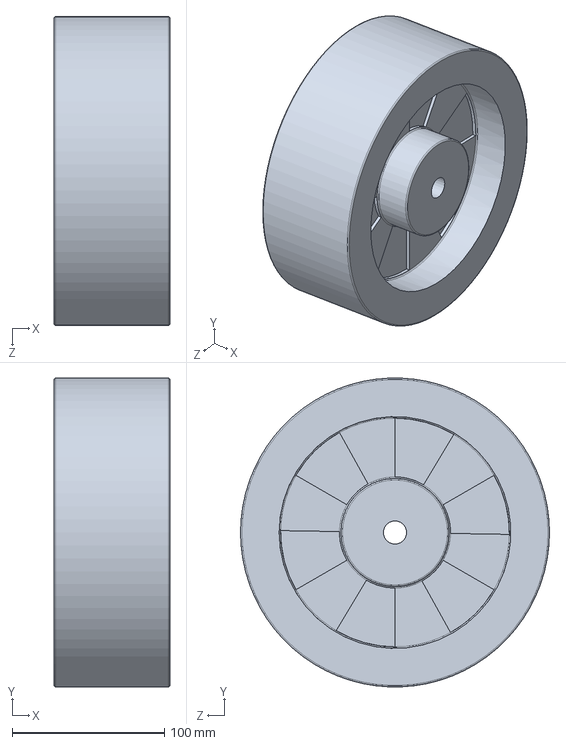
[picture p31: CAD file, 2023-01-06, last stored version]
CAD_Model/Wheels.SLDPRT
76.2 x 203.0 x 203.2 mm

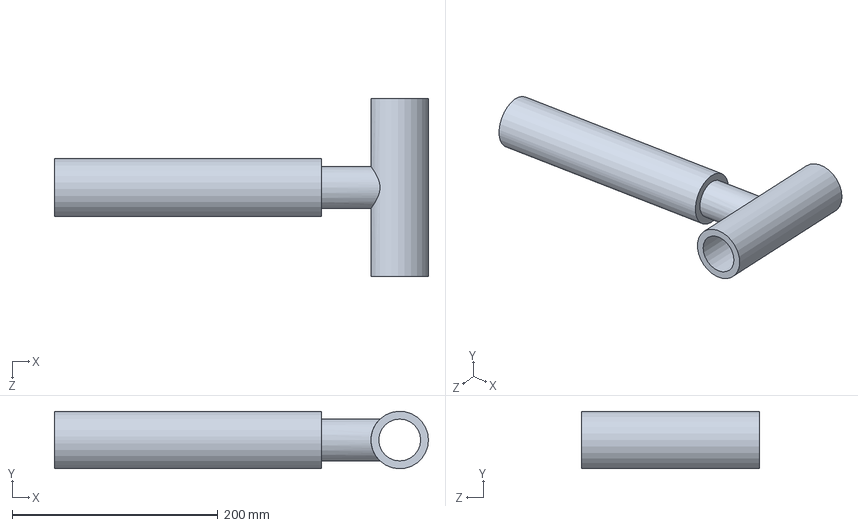
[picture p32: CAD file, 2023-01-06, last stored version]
CAD_Model/link4.SLDPRT
363.2 x 55.8 x 172.7 mm

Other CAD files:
transformer/meshes/FR_axle.STL
transformer/meshes/BR_wheel.STL
transformer/meshes/BR_axle.STL
transformer/meshes/FL_wheel.STL
CAD_Model/Axle.SLDPRT
CAD_Model/finger.SLDPRT
CAD_Model/link1_old.SLDPRT
CAD_Model/link2.SLDPRT
CAD_Model/link3.SLDPRT
CAD_Model/link4____notused.SLDPRT
CAD_Model/rotating_base.SLDPRT
transformer/meshes/BL_axle.STL
transformer/meshes/FR_wheel.STL
transformer/meshes/base_link.STL
transformer/meshes/finger2.STL
transformer/meshes/mlr_link2.STL
transformer/meshes/mlr_link4.STL
transformer/meshes/mlr_link5.STL
transformer/meshes/mlr_link6.STL

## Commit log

2022-12-15 Added URDF + ROS package of Transformer Robot
2022-12-15 Added CAD model of the Transformer Robot
2022-12-15 Added CAD model of Transformer Robot
2023-01-06 Refactoring the repo
    [Axle.SLDPRT, BL_axle.STL, BL_wheel.STL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]
2023-01-06 Create scripts pls
    [Axle.SLDPRT, BL_axle.STL, BL_wheel.STL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]
